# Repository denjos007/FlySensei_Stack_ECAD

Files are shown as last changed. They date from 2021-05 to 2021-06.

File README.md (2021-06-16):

PCB design of stackable controllers for blimps

Each stack contains a specified function for controlling a blimp

# Stacks
Below is the description of each stack

## RPi Stack
This stack takes care of the vision system for the blimp. The hardware integrates a Raspberry Pi CM4 with a Google Coral Accelerator Module. This combination will connect to upto 3 external cameras and process the image information. The system can implement machine vision algorithms like YOLO to process the scene and extract relevent information. 

## Actuation Stack

## Realtime Stack

## Sensing Stack

## Communication Stack

# Contributors
Joseph Prince Mathew - jprincem@masonlive.gmu.edu

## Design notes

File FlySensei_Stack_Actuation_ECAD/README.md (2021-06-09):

Actuation stack for the stackable blimp controller

# Functional Specifications
- PWM driver: PCA9685BS 16 channel 
- I2C control input with selectable channels
- 2S 3S and 4S LiPo input voltage capability
- 8 Servo channels with 5V power
- 8 BLDC or 4 Brushed motor channels with direct VBATT
- Optional 2S battery monitor: MAX17049G+T10
- Optional high current solder points for battery input

# Caution
- Check battery polarity before inserting the connecting the lipo battery
- When using 3S or higher voltage battery, remove the attached fuel gauge IC. Its rated only for 2S

# Contributors
Joseph Prince Mathew - jprincem@masonlive.gmu.edu

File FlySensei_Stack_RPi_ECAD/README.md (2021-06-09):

Stackable base board for the Raspberry Pi CM4 with an integrated AI co-processor

# Functional Specifications
- Raspberry Pi CM4 used as the main processor
- Google Coral used as the AI co-processor
- Selectable Power input from USB-C port and Battery input from stack headers
- Ethernet and camera FFC ports

# Contributors
Joseph Prince Mathew - jprincem@masonlive.gmu.edu

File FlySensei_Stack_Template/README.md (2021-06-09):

Template of the stack

Each stack contains 2x 20 pin connector with male pins on the top and the female pins on the bottom

# Usage

- Create a new PCB project in KiCAD
- Copy the schematic file and the PCB file to the project
- Rename the PCB file to the same name as the project
- Add the schematic of the connector to the main sheet as a hierarchical sheet

# Contributors
Joseph Prince Mathew - jprincem@masonlive.gmu.edu

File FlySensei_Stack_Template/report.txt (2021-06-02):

Info: Processing symbol 'C1:Capacitor_SMD:C_0402_1005Metric'.
Info: Processing symbol 'U16:Package_SO:SOIC-8-1EP_3.9x4.9mm_P1.27mm_EP2.95x4.9mm_Mask2.71x3.4mm_ThermalVias'.
Info: Processing symbol 'U10:Package_TO_SOT_SMD:SOT-23-5'.
Info: Processing symbol 'U9:Package_SON:USON-10_2.5x1.0mm_P0.5mm'.
Info: Processing symbol 'U8:Package_SON:USON-10_2.5x1.0mm_P0.5mm'.
Info: Processing symbol 'U7:Package_DFN_QFN_U:MPM3610_QFN-20_5x3mm'.
Info: Processing symbol 'U6:Package_DFN_QFN:Texas_X2QFN-12_1.6x1.6mm_P0.4mm'.
Info: Processing symbol 'U5:Package_TO_SOT_SMD:Texas_DRT-3'.
Info: Processing symbol 'C2:Capacitor_SMD:C_0402_1005Metric'.
Info: Processing symbol 'U4:AI_Coral:G313-06329-00'.
Info: Processing symbol 'U3:Package_TO_SOT_SMD:SOT-353_SC-70-5'.
Info: Processing symbol 'U2:Package_SO:SOIC-8W_5.3x5.3mm_P1.27mm'.
Info: Processing symbol 'U1:RPi_CM4IO:Raspberry-Pi-4-Compute-Module'.
Info: Processing symbol 'TP6:TestPoint:TestPoint_Pad_2.0x2.0mm'.
Info: Processing symbol 'TP4:TestPoint:TestPoint_Pad_2.0x2.0mm'.
Info: Processing symbol 'SW3:Button_Switch_SMD:SW_SPDT_PCM12'.
Info: Processing symbol 'C3:Capacitor_SMD:C_0402_1005Metric'.
Info: Processing symbol 'SW2:Button_Switch_SMD:SW_SPDT_PCM12'.
Info: Processing symbol 'SW1:Button_Switch_SMD:Panasonic_EVQPUL_EVQPUC'.
Info: Processing symbol 'R21:Resistor_SMD:R_0402_1005Metric'.
Info: Processing symbol 'R20:Resistor_SMD:R_0402_1005Metric'.
Info: Processing symbol 'R19:Resistor_SMD:R_0402_1005Metric'.
Info: Processing symbol 'R18:Resistor_SMD:R_0402_1005Metric'.
Info: Processing symbol 'R17:Resistor_SMD:R_0402_1005Metric'.
Info: Processing symbol 'C4:Capacitor_SMD:C_0402_1005Metric'.
Info: Processing symbol 'R16:Resistor_SMD:R_0402_1005Metric'.
Info: Processing symbol 'R15:Resistor_SMD:R_0402_1005Metric'.
Info: Processing symbol 'R14:Resistor_SMD:R_0402_1005Metric'.
Info: Processing symbol 'R13:Resistor_SMD:R_0402_1005Metric'.
Info: Processing symbol 'R12:Resistor_SMD:R_0402_1005Metric'.
Info: Processing symbol 'R11:Resistor_SMD:R_0402_1005Metric'.
Info: Processing symbol 'R10:Resistor_SMD:R_0402_1005Metric'.
Info: Processing symbol 'C5:Capacitor_SMD:C_0402_1005Metric'.
Info: Processing symbol 'R9:Resistor_SMD:R_0402_1005Metric'.
Info: Processing symbol 'R8:Resistor_SMD:R_0402_1005Metric'.
Info: Processing symbol 'R6:Resistor_SMD:R_0402_1005Metric'.
Info: Processing symbol 'R5:Resistor_SMD:R_0402_1005Metric'.
Info: Processing symbol 'R4:Resistor_SMD:R_0402_1005Metric'.
Info: Processing symbol 'R3:Resistor_SMD:R_0402_1005Metric'.
Info: Processing symbol 'R2:Resistor_SMD:R_0402_1005Metric'.
Info: Processing symbol 'C6:Capacitor_SMD:C_0402_1005Metric'.
Info: Processing symbol 'R1:Resistor_SMD:R_0402_1005Metric'.
Info: Processing symbol 'Q1:Package_TO_SOT_SMD:SOT-23'.
Info: Processing symbol 'L1:Inductor_SMD:L_Bourns_SRN6045TA'.
Info: Processing symbol 'JP6:Jumper:SolderJumper-2_P1.3mm_Open_RoundedPad1.0x1.5mm'.
Info: Processing symbol 'JP5:Jumper:SolderJumper-2_P1.3mm_Open_RoundedPad1.0x1.5mm'.
Info: Processing symbol 'JP4:Jumper:SolderJumper-2_P1.3mm_Open_RoundedPad1.0x1.5mm'.
Info: Processing symbol 'JP3:Jumper:SolderJumper-2_P1.3mm_Open_RoundedPad1.0x1.5mm'.
Info: Processing symbol 'C7:Capacitor_SMD:C_0402_1005Metric'.
Info: Processing symbol 'JP2:Jumper:SolderJumper-2_P1.3mm_Open_RoundedPad1.0x1.5mm'.
Info: Processing symbol 'JP1:Jumper:SolderJumper-2_P1.3mm_Open_RoundedPad1.0x1.5mm'.
Info: Processing symbol 'J10:CM4IO:SDCARD_MOLEX_503398-1892'.
Info: Processing symbol 'J9:Connector_FFC-FPC:Hirose_FH12-14S-0.5SH_1x14-1MP_P0.50mm_Horizontal'.
Info: Processing symbol 'J8:Connector_FFC-FPC:Hirose_FH12-22S-0.5SH_1x22-1MP_P0.50mm_Horizontal'.
Info: Processing symbol 'J7:Connector_FFC-FPC:Hirose_FH12-22S-0.5SH_1x22-1MP_P0.50mm_Horizontal'.
Info: Processing symbol 'J6:Connector_PinHeader_1.27mm:PinHeader_1x20_P1.27mm_Vertical_SMD_Pin1Left'.
Info: Processing symbol 'C8:Capacitor_SMD:C_0402_1005Metric'.
Info: Processing symbol 'J5:Connector_PinHeader_1.27mm:PinHeader_1x20_P1.27mm_Vertical_SMD_Pin1Right'.
Info: Processing symbol 'J4:Connector_PinHeader_1.27mm:PinHeader_1x20_P1.27mm_Vertical_SMD_Pin1Left'.
Info: Processing symbol 'J3:Connector_PinHeader_1.27mm:PinHeader_1x20_P1.27mm_Vertical_SMD_Pin1Right'.
Info: Processing symbol 'R7:Resistor_SMD:R_0402_1005Metric'.
Info: Processing symbol 'J2:Connector_USB:USB_C_Receptacle_XKB_U262-16XN-4BVC11'.
Info: Processing symbol 'J1:Connector_PinHeader_1.00mm:PinHeader_1x03_P1.00mm_Vertical'.
Info: Processing symbol 'D8:LED_SMD:LED_0603_1608Metric'.
Info: Processing symbol 'C9:Capacitor_SMD:C_0402_1005Metric'.
Info: Processing symbol 'D7:Diode_SMD:D_SMB'.
Info: Processing symbol 'D6:Diode_SMD:D_SMB'.
Info: Processing symbol 'D5:Diode_SMD:D_SMB'.
Info: Processing symbol 'D4:LED_SMD:LED_0603_1608Metric'.
Info: Processing symbol 'D3:LED_SMD:LED_0603_1608Metric'.
Info: Processing symbol 'D2:LED_SMD:LED_0603_1608Metric'.
Info: Processing symbol 'D1:LED_SMD:LED_0603_1608Metric'.
Info: Processing symbol 'C10:Capacitor_SMD:C_0402_1005Metric'.
Info: Processing symbol 'C27:Capacitor_SMD:C_0805_2012Metric'.
Info: Processing symbol 'C26:Capacitor_SMD:C_0805_2012Metric'.
Info: Processing symbol 'C25:Capacitor_SMD:C_0805_2012Metric'.
Info: Processing symbol 'C24:Capacitor_SMD:C_0805_2012Metric'.
Info: Processing symbol 'C23:Capacitor_SMD:C_0805_2012Metric'.
Info: Processing symbol 'C22:Capacitor_SMD:C_0402_1005Metric'.
Info: Processing symbol 'C21:Capacitor_SMD:C_0402_1005Metric'.
Info: Processing symbol 'C11:Capacitor_SMD:C_0603_1608Metric'.
Info: Processing symbol 'C20:Capacitor_SMD:C_0402_1005Metric'.
Info: Processing symbol 'C19:Capacitor_SMD:C_0603_1608Metric'.
Info: Processing symbol 'C18:Capacitor_Tantalum_SMD:CP_EIA-7343-31_Kemet-D'.
Info: Processing symbol 'C17:Capacitor_SMD:C_0402_1005Metric'.
Info: Processing symbol 'C16:Capacitor_SMD:C_0603_1608Metric'.
Info: Processing symbol 'C15:Capacitor_SMD:C_0402_1005Metric'.
Info: Processing symbol 'C14:Capacitor_SMD:C_0805_2012Metric'.
Info: Processing symbol 'C12:Capacitor_SMD:C_0603_1608Metric'.
Info: Processing symbol 'C13:Capacitor_SMD:C_0805_2012Metric'.
Changed REF** reference designator to C12.
Changed C12 value from C_0603_1608Metric to 1u 16V.
Updated C12 symbol association from  to /057c2e08-823a-4406-b5ca-db4e8c27b194/d5c9fad7-bc46-4f83-bd64-f66f1dbcdc59.
Updated C12 properties.
Connected C12 pin 1 to +5V.
Connected C12 pin 2 to GND.
Added C12 (footprint "Capacitor_SMD:C_0603_1608Metric").
Added C13 (footprint "Capacitor_SMD:C_0805_2012Metric").
Changed REF** reference designator to C13.
Changed C13 value from C_0805_2012Metric to 10u 35v.
Updated C13 symbol association from  to /0cf2b8c0-70f6-4976-95f7-88ea6c192189/00000000-0000-0000-0000-00005eb56b99.
Updated C13 properties.
Connected C13 pin 1 to +BATT.
Connected C13 pin 2 to GND.
Connected C11 pin 2 to GND.
Added C14 (footprint "Capacitor_SMD:C_0805_2012Metric").
Changed REF** reference designator to C14.
Changed C14 value from C_0805_2012Metric to 10u 35v.
Updated C14 symbol association from  to /0cf2b8c0-70f6-4976-95f7-88ea6c192189/00000000-0000-0000-0000-00005eb4cf69.
Updated C14 properties.
Connected C14 pin 1 to +BATT.
Connected C14 pin 2 to GND.
Connected C11 pin 1 to Net-(C11-Pad1).
Added C15 (footprint "Capacitor_SMD:C_0402_1005Metric").
Changed REF** reference designator to C15.
Changed C15 value from C_0402_1005Metric to 100n 35V.
Updated C15 symbol association from  to /0cf2b8c0-70f6-4976-95f7-88ea6c192189/00000000-0000-0000-0000-00005e540df2.
Updated C15 properties.
Connected C15 pin 1 to Net-(C15-Pad1).
Connected C15 pin 2 to Net-(C15-Pad2).
Updated C11 properties.
Added C16 (footprint "Capacitor_SMD:C_0603_1608Metric").
Changed REF** reference designator to C16.
Changed C16 value from C_0603_1608Metric to 10u 35V.
Updated C16 symbol association from  to /0cf2b8c0-70f6-4976-95f7-88ea6c192189/0d5ad291-fce2-4c53-b48f-1c66806904ff.
Updated C16 properties.
Connected C16 pin 1 to +BATT.
Connected C16 pin 2 to GND.
Updated C11 symbol association from  to /057c2e08-823a-4406-b5ca-db4e8c27b194/cf37d5d3-b56f-4aae-943b-4b63578a7e71.
Added C17 (footprint "Capacitor_SMD:C_0402_1005Metric").
Changed REF** reference designator to C17.
Changed C17 value from C_0402_1005Metric to 100n 35V.
Updated C17 symbol association from  to /0cf2b8c0-70f6-4976-95f7-88ea6c192189/00000000-0000-0000-0000-00005e540dfb.
Updated C17 properties.
Connected C17 pin 1 to Net-(C17-Pad1).
Connected C17 pin 2 to GND.
Changed C11 value from C_0603_1608Metric to 22u 16V.
Added C18 (footprint "Capacitor_Tantalum_SMD:CP_EIA-7343-31_Kemet-D").
Changed REF** reference designator to C18.
Changed C18 value from CP_EIA-7343-31_Kemet-D to 100uF.
Updated C18 symbol association from  to /0cf2b8c0-70f6-4976-95f7-88ea6c192189/37be3783-986e-41bc-a074-efadea452183.
Updated C18 properties.
Connected C18 pin 1 to Net-(C18-Pad1).
Connected C18 pin 2 to GND.
Changed REF** reference designator to C11.
Added C19 (footprint "Capacitor_SMD:C_0603_1608Metric").
Changed REF** reference designator to C19.
Changed C19 value from C_0603_1608Metric to 22u 16V.
Updated C19 symbol association from  to /0cf2b8c0-70f6-4976-95f7-88ea6c192189/f4fe2ad8-9f7d-486e-9b01-b41b7db66e44.
Updated C19 properties.
Connected C19 pin 1 to +3V3.
Connected C19 pin 2 to GND.
Added C11 (footprint "Capacitor_SMD:C_0603_1608Metric").
Added C20 (footprint "Capacitor_SMD:C_0402_1005Metric").
Changed REF** reference designator to C20.
Changed C20 value from C_0402_1005Metric to 1nf 16V.
Updated C20 symbol association from  to /0cf2b8c0-70f6-4976-95f7-88ea6c192189/00000000-0000-0000-0000-00005e540df8.
Updated C20 properties.
Connected C20 pin 1 to Net-(C20-Pad1).
Connected C20 pin 2 to GND.
Connected C10 pin 2 to GND.
Added C21 (footprint "Capacitor_SMD:C_0402_1005Metric").
Changed REF** reference designator to C21.
Changed C21 value from C_0402_1005Metric to 1.2nF 16V.
Updated C21 symbol association from  to /0cf2b8c0-70f6-4976-95f7-88ea6c192189/00000000-0000-0000-0000-00005e540df7.
Updated C21 properties.
Connected C21 pin 1 to Net-(C21-Pad1).
Connected C21 pin 2 to GND.
Connected C10 pin 1 to +3V3.
Added C22 (footprint "Capacitor_SMD:C_0402_1005Metric").
Changed REF** reference designator to C22.
Changed C22 value from C_0402_1005Metric to 1nf 16V.
Updated C22 symbol association from  to /0cf2b8c0-70f6-4976-95f7-88ea6c192189/00000000-0000-0000-0000-00005e540df4.
Updated C22 properties.
Connected C22 pin 1 to Net-(C18-Pad1).
Connected C22 pin 2 to Net-(C22-Pad2).
Updated C10 properties.
Added C23 (footprint "Capacitor_SMD:C_0805_2012Metric").
Changed REF** reference designator to C23.
Changed C23 value from C_0805_2012Metric to 22u 16V.
Updated C23 symbol association from  to /0cf2b8c0-70f6-4976-95f7-88ea6c192189/00000000-0000-0000-0000-00005d3289ab.
Updated C23 properties.
Connected C23 pin 1 to Net-(C18-Pad1).
Connected C23 pin 2 to GND.
Updated C10 symbol association from  to /c7aadd96-de8c-4974-aee8-6d5527743de5/b0267f50-fd0c-4a5f-b7d1-92f9a74be421.
Added C24 (footprint "Capacitor_SMD:C_0805_2012Metric").
Changed REF** reference designator to C24.
Changed C24 value from C_0805_2012Metric to 22u 16V.
Updated C24 symbol association from  to /0cf2b8c0-70f6-4976-95f7-88ea6c192189/00000000-0000-0000-0000-00005d3289b2.
Updated C24 properties.
Connected C24 pin 1 to Net-(C18-Pad1).
Connected C24 pin 2 to GND.
Changed C10 value from C_0402_1005Metric to 0u1 6.3V.
Added C25 (footprint "Capacitor_SMD:C_0805_2012Metric").
Changed REF** reference designator to C25.
Changed C25 value from C_0805_2012Metric to 22u 16V.
Updated C25 symbol association from  to /0cf2b8c0-70f6-4976-95f7-88ea6c192189/00000000-0000-0000-0000-00005d3289b8.
Updated C25 properties.
Connected C25 pin 1 to Net-(C18-Pad1).
Connected C25 pin 2 to GND.
Changed REF** reference designator to C10.
Added C26 (footprint "Capacitor_SMD:C_0805_2012Metric").
Changed REF** reference designator to C26.
Changed C26 value from C_0805_2012Metric to 22u.
Updated C26 symbol association from  to /f22911d6-fd0b-420b-886b-10dcff84029c/93127e37-2f19-438d-a456-8a96f2977297.
Updated C26 properties.
Connected C26 pin 1 to +BATT.
Connected C26 pin 2 to GND.
Added C10 (footprint "Capacitor_SMD:C_0402_1005Metric").
Added C27 (footprint "Capacitor_SMD:C_0805_2012Metric").
Changed REF** reference designator to C27.
Changed C27 value from C_0805_2012Metric to 10u.
Updated C27 symbol association from  to /b1d9abd2-56b2-476f-ba8d-e6505e2da0de/7aa47e22-220a-48de-a0dc-e60b4a80156a.
Updated C27 properties.
Connected C27 pin 1 to /SD Card/SD_PWR.
Connected C27 pin 2 to GND.
Connected C9 pin 2 to GND.
Added D1 (footprint "LED_SMD:LED_0603_1608Metric").
Changed REF** reference designator to D1.
Changed D1 value from LED_0603_1608Metric to LED_GRN.
Updated D1 symbol association from  to /93e7d8cf-e360-4b54-86be-d58fb9455bdf/d052e667-c78d-4c60-9067-dea9ab9f9831.
Updated D1 properties.
Connected D1 pin 1 to Net-(D1-Pad1).
Connected D1 pin 2 to +3V3_RPI.
Connected C9 pin 1 to +3V3.
Added D2 (footprint "LED_SMD:LED_0603_1608Metric").
Changed REF** reference designator to D2.
Changed D2 value from LED_0603_1608Metric to LED_GRN.
Updated D2 symbol association from  to /93e7d8cf-e360-4b54-86be-d58fb9455bdf/5d8d864f-70b6-4a40-8cab-c69691953af5.
Updated D2 properties.
Connected D2 pin 1 to Net-(D2-Pad1).
Connected D2 pin 2 to +3V3_RPI.
Updated C9 properties.
Added D3 (footprint "LED_SMD:LED_0603_1608Metric").
Changed REF** reference designator to D3.
Changed D3 value from LED_0603_1608Metric to LED_AMB.
Updated D3 symbol association from  to /93e7d8cf-e360-4b54-86be-d58fb9455bdf/27de79ba-83bf-482b-9f05-30a12075cb2a.
Updated D3 properties.
Connected D3 pin 1 to Net-(D3-Pad1).
Connected D3 pin 2 to +3V3_RPI.
Updated C9 symbol association from  to /c7aadd96-de8c-4974-aee8-6d5527743de5/035c14f8-ab75-4ff6-90a5-e33b5679a37f.
Added D4 (footprint "LED_SMD:LED_0603_1608Metric").
Changed REF** reference designator to D4.
Changed D4 value from LED_0603_1608Metric to LED_RED.
Updated D4 symbol association from  to /93e7d8cf-e360-4b54-86be-d58fb9455bdf/b7a968bb-c5ee-44dd-8959-c6f6e151e9ab.
Updated D4 properties.
Connected D4 pin 1 to Net-(D4-Pad1).
Connected D4 pin 2 to +3V3_RPI.
Changed C9 value from C_0402_1005Metric to 0u1 6.3V.
Added D5 (footprint "Diode_SMD:D_SMB").
Changed REF** reference designator to D5.
Changed D5 value from D_SMB to D_Schottky.
Updated D5 symbol association from  to /057c2e08-823a-4406-b5ca-db4e8c27b194/81568044-992c-48f2-a54a-9e9377f4d5ae.
Updated D5 properties.
Connected D5 pin 1 to +5V.
Connected D5 pin 2 to Net-(C11-Pad1).
Changed REF** reference designator to C9.
Added D6 (footprint "Diode_SMD:D_SMB").
Changed REF** reference designator to D6.
Changed D6 value from D_SMB to D_Schottky.
Updated D6 symbol association from  to /0cf2b8c0-70f6-4976-95f7-88ea6c192189/ed8ba917-dfd4-4435-9898-75160a2297d1.
Updated D6 properties.
Connected D6 pin 1 to +5V.
Connected D6 pin 2 to Net-(C18-Pad1).
Added C9 (footprint "Capacitor_SMD:C_0402_1005Metric").
Added D7 (footprint "Diode_SMD:D_SMB").
Changed REF** reference designator to D7.
Changed D7 value from D_SMB to D_Schottky.
Updated D7 symbol association from  to /f22911d6-fd0b-420b-886b-10dcff84029c/0b2db708-50f7-447f-92a1-9296f2459b91.
Updated D7 properties.
Connected D7 pin 1 to +BATT.
Connected D7 pin 2 to /Stacking Connectors/BATT_IN.
Connected C8 pin 2 to GND.
Added D8 (footprint "LED_SMD:LED_0603_1608Metric").
Changed REF** reference designator to D8.
Changed D8 value from LED_0603_1608Metric to W_LED.
Updated D8 symbol association from  to /93e7d8cf-e360-4b54-86be-d58fb9455bdf/5fc6c698-fa36-406b-8e10-f746facb42c5.
Updated D8 properties.
Connected D8 pin 1 to Net-(D8-Pad1).
Connected D8 pin 2 to Net-(D8-Pad2).
Connected C8 pin 1 to +3V3.
Added J1 (footprint "Connector_PinHeader_1.00mm:PinHeader_1x03_P1.00mm_Vertical").
Changed REF** reference designator to J1.
Changed J1 value from PinHeader_1x03_P1.00mm_Vertical to Conn_01x03.
Updated J1 symbol association from  to /93e7d8cf-e360-4b54-86be-d58fb9455bdf/e53ead3b-26db-4a23-bd2d-10031139ddc5.
Updated J1 properties.
Connected J1 pin 1 to /RPi_CM4/RPI_RUN_PG.
Connected J1 pin 2 to GND.
Connected J1 pin 3 to /RPi_CM4/RPI_GLOBL_EN.
Updated C8 properties.
Added J2 (footprint "Connector_USB:USB_C_Receptacle_XKB_U262-16XN-4BVC11").
Changed REF** reference designator to J2.
Changed J2 value from USB_C_Receptacle_XKB_U262-16XN-4BVC11 to USB_C_Receptacle_USB2.0.
Updated J2 symbol association from  to /057c2e08-823a-4406-b5ca-db4e8c27b194/14bf70aa-48dc-42ff-af02-dd620e4b800d.
Updated J2 properties.
Connected J2 pin S1 to unconnected-(J2-PadS1).
Connected J2 pin S1 to unconnected-(J2-PadS1).
Connected J2 pin S1 to unconnected-(J2-PadS1).
Connected J2 pin S1 to unconnected-(J2-PadS1).
Connected J2 pin B1 to GND.
Connected J2 pin B4 to Net-(C11-Pad1).
Connected J2 pin B5 to Net-(J2-PadB5).
Connected J2 pin A8 to unconnected-(J2-PadA8).
Connected J2 pin B6 to /RPi_CM4/USB_DP.
Connected J2 pin A7 to /RPi_CM4/USB_DN.
Connected J2 pin A6 to /RPi_CM4/USB_DP.
Connected J2 pin B7 to /RPi_CM4/USB_DN.
Connected J2 pin A5 to Net-(J2-PadA5).
Updated C8 symbol association from  to /c7aadd96-de8c-4974-aee8-6d5527743de5/35e6c8af-12af-4b13-9694-213bb1cf0153.
Connected J2 pin A4 to Net-(C11-Pad1).
Connected J2 pin A1 to GND.
Connected J2 pin B12 to GND.
Connected J2 pin B9 to Net-(C11-Pad1).
Connected J2 pin A9 to Net-(C11-Pad1).
Connected J2 pin A12 to GND.
Changed C8 value from C_0402_1005Metric to 0u1 6.3V.
Added J3 (footprint "Connector_PinHeader_1.27mm:PinHeader_1x20_P1.27mm_Vertical_SMD_Pin1Right").
Changed REF** reference designator to J3.
Changed J3 value from PinHeader_1x20_P1.27mm_Vertical_SMD_Pin1Right to Conn_01x20_Female.
Updated J3 symbol association from  to /f22911d6-fd0b-420b-886b-10dcff84029c/730ab321-7c86-4037-aece-98780bac3f9a.
Updated J3 properties.
Connected J3 pin 2 to /Stacking Connectors/BATT_IN.
Connected J3 pin 4 to GND.
Connected J3 pin 6 to /RPi_CM4/GPIO_1.
Connected J3 pin 8 to /RPi_CM4/SPI0.MISO.
Connected J3 pin 10 to /RPi_CM4/SPI0.CS0.
Connected J3 pin 12 to /RPi_CM4/SPI0.CS2.
Connected J3 pin 14 to GND.
Connected J3 pin 16 to /RPi_CM4/SPI1.MISO.
Connected J3 pin 18 to /RPi_CM4/SPI1.CS0.
Connected J3 pin 20 to GND.
Connected J3 pin 1 to /Stacking Connectors/BATT_IN.
Connected J3 pin 3 to GND.
Connected J3 pin 5 to /RPi_CM4/GPIO_0.
Connected J3 pin 7 to /RPi_CM4/SPI0.MOSI.
Connected J3 pin 9 to /RPi_CM4/SPI0.CLK.
Connected J3 pin 11 to /RPi_CM4/SPI0.CS1.
Connected J3 pin 13 to /RPi_CM4/SPI0.CS3.
Connected J3 pin 15 to /RPi_CM4/SPI1.MOSI.
Connected J3 pin 17 to /RPi_CM4/SPI1.CLK.
Connected J3 pin 19 to /RPi_CM4/SPI1.CS1.
Changed REF** reference designator to C8.
Added J4 (footprint "Connector_PinHeader_1.27mm:PinHeader_1x20_P1.27mm_Vertical_SMD_Pin1Left").
Changed REF** reference designator to J4.
Changed J4 value from PinHeader_1x20_P1.27mm_Vertical_SMD_Pin1Left to Conn_01x20_Male.
Updated J4 symbol association from  to /f22911d6-fd0b-420b-886b-10dcff84029c/8999cfdc-1a52-4c6c-8d6f-7db9d488c1ed.
Updated J4 properties.
Connected J4 pin 1 to /Stacking Connectors/BATT_IN.
Connected J4 pin 3 to GND.
Connected J4 pin 5 to /RPi_CM4/GPIO_0.
Connected J4 pin 7 to /RPi_CM4/SPI0.MOSI.
Connected J4 pin 9 to /RPi_CM4/SPI0.CLK.
Connected J4 pin 11 to /RPi_CM4/SPI0.CS1.
Connected J4 pin 13 to /RPi_CM4/SPI0.CS3.
Connected J4 pin 15 to /RPi_CM4/SPI1.MOSI.
Connected J4 pin 17 to /RPi_CM4/SPI1.CLK.
Connected J4 pin 19 to /RPi_CM4/SPI1.CS1.
Connected J4 pin 2 to /Stacking Connectors/BATT_IN.
Connected J4 pin 4 to GND.
Connected J4 pin 6 to /RPi_CM4/GPIO_1.
Connected J4 pin 8 to /RPi_CM4/SPI0.MISO.
Connected J4 pin 10 to /RPi_CM4/SPI0.CS0.
Connected J4 pin 12 to /RPi_CM4/SPI0.CS2.
Connected J4 pin 14 to GND.
Connected J4 pin 16 to /RPi_CM4/SPI1.MISO.
Connected J4 pin 18 to /RPi_CM4/SPI1.CS0.
Connected J4 pin 20 to GND.
Added C8 (footprint "Capacitor_SMD:C_0402_1005Metric").
Added J5 (footprint "Connector_PinHeader_1.27mm:PinHeader_1x20_P1.27mm_Vertical_SMD_Pin1Right").
Changed REF** reference designator to J5.
Changed J5 value from PinHeader_1x20_P1.27mm_Vertical_SMD_Pin1Right to Conn_01x20_Female.
Updated J5 symbol association from  to /f22911d6-fd0b-420b-886b-10dcff84029c/7beed154-96e9-49c8-b518-4b3691163b95.
Updated J5 properties.
Connected J5 pin 2 to /Stacking Connectors/BATT_IN.
Connected J5 pin 4 to GND.
Connected J5 pin 6 to /RPi_CM4/GPIO_3.
Connected J5 pin 8 to /RPi_CM4/GPIO_5.
Connected J5 pin 10 to /RPi_CM4/GPIO_7.
Connected J5 pin 12 to /RPi_CM4/I2C0.SCL.
Connected J5 pin 14 to /Stacking Connectors/I2C1.SCL.
Connected J5 pin 16 to GND.
Connected J5 pin 18 to /RPi_CM4/UART0.RX.
Connected J5 pin 20 to /RPi_CM4/UART1.RX.
Connected J5 pin 1 to /Stacking Connectors/BATT_IN.
Connected J5 pin 3 to GND.
Connected J5 pin 5 to /RPi_CM4/GPIO_2.
Connected J5 pin 7 to /RPi_CM4/GPIO_4.
Connected J5 pin 9 to /RPi_CM4/GPIO_6.
Connected J5 pin 11 to GND.
Connected J5 pin 13 to /RPi_CM4/I2C0.SDA.
Connected J5 pin 15 to /Stacking Connectors/I2C1.SDA.
Connected J5 pin 17 to /RPi_CM4/UART0.TX.
Connected J5 pin 19 to /RPi_CM4/UART1.TX.
Connected C7 pin 2 to GND.
Added J6 (footprint "Connector_PinHeader_1.27mm:PinHeader_1x20_P1.27mm_Vertical_SMD_Pin1Left").
Changed REF** reference designator to J6.
Changed J6 value from PinHeader_1x20_P1.27mm_Vertical_SMD_Pin1Left to Conn_01x20_Male.
Updated J6 symbol association from  to /f22911d6-fd0b-420b-886b-10dcff84029c/d6cef596-d8af-42ab-a0b6-04219f1f1742.
Updated J6 properties.
Connected J6 pin 1 to /Stacking Connectors/BATT_IN.
Connected J6 pin 3 to GND.
Connected J6 pin 5 to /RPi_CM4/GPIO_2.
Connected J6 pin 7 to /RPi_CM4/GPIO_4.
Connected J6 pin 9 to /RPi_CM4/GPIO_6.
Connected J6 pin 11 to GND.
Connected J6 pin 13 to /RPi_CM4/I2C0.SDA.
Connected J6 pin 15 to /Stacking Connectors/I2C1.SDA.
Connected J6 pin 17 to /RPi_CM4/UART0.TX.
Connected J6 pin 19 to /RPi_CM4/UART1.TX.
Connected J6 pin 2 to /Stacking Connectors/BATT_IN.
Connected J6 pin 4 to GND.
Connected J6 pin 6 to /RPi_CM4/GPIO_3.
Connected J6 pin 8 to /RPi_CM4/GPIO_5.
Connected J6 pin 10 to /RPi_CM4/GPIO_7.
Connected J6 pin 12 to /RPi_CM4/I2C0.SCL.
Connected J6 pin 14 to /Stacking Connectors/I2C1.SCL.
Connected J6 pin 16 to GND.
Connected J6 pin 18 to /RPi_CM4/UART0.RX.
Connected J6 pin 20 to /RPi_CM4/UART1.RX.
Connected C7 pin 1 to +3V3.
Added J7 (footprint "Connector_FFC-FPC:Hirose_FH12-22S-0.5SH_1x22-1MP_P0.50mm_Horizontal").
Changed REF** reference designator to J7.
Changed J7 value from Hirose_FH12-22S-0.5SH_1x22-1MP_P0.50mm_Horizontal to Conn_01x22_Female.
Updated J7 symbol association from  to /1a1df624-ea52-444e-8eb0-2f13ef4aac9c/b3fac725-0c5e-42cc-9b85-f37d2753b6b5.
Updated J7 properties.
Connected J7 pin 1 to GND.
Connected J7 pin 2 to /High Speed Interfaces/CAM0_MIPI.D0_N.
Connected J7 pin 3 to /High Speed Interfaces/CAM0_MIPI.D0_P.
Connected J7 pin 4 to GND.
Connected J7 pin 5 to /High Speed Interfaces/CAM0_MIPI.D1_N.
Connected J7 pin 6 to /High Speed Interfaces/CAM0_MIPI.D1_P.
Connected J7 pin 7 to GND.
Connected J7 pin 8 to /High Speed Interfaces/CAM0_MIPI.C_N.
Connected J7 pin 9 to /High Speed Interfaces/CAM0_MIPI.C_P.
Connected J7 pin 10 to GND.
Connected J7 pin 11 to unconnected-(J7-Pad11).
Connected J7 pin 12 to unconnected-(J7-Pad12).
Connected J7 pin 13 to GND.
Connected J7 pin 14 to unconnected-(J7-Pad14).
Connected J7 pin 15 to unconnected-(J7-Pad15).
Connected J7 pin 16 to GND.
Connected J7 pin 17 to /High Speed Interfaces/CAM_GPIO.
Connected J7 pin 18 to unconnected-(J7-Pad18).
Connected J7 pin 19 to GND.
Connected J7 pin 20 to /High Speed Interfaces/CAM0_SCL.
Connected J7 pin 21 to /High Speed Interfaces/CAM0_SDA.
Connected J7 pin 22 to +3V3.
Updated C7 properties.
Added J8 (footprint "Connector_FFC-FPC:Hirose_FH12-22S-0.5SH_1x22-1MP_P0.50mm_Horizontal").
Changed REF** reference designator to J8.
Changed J8 value from Hirose_FH12-22S-0.5SH_1x22-1MP_P0.50mm_Horizontal to Conn_01x22_Female.
Updated J8 symbol association from  to /1a1df624-ea52-444e-8eb0-2f13ef4aac9c/320604ed-1bea-420b-bb1c-2d498855f18f.
Updated J8 properties.
Connected J8 pin 1 to GND.
Connected J8 pin 2 to /High Speed Interfaces/CAM1_MIPI.D0_N.
Connected J8 pin 3 to /High Speed Interfaces/CAM1_MIPI.D0_P.
Connected J8 pin 4 to GND.
Connected J8 pin 5 to /High Speed Interfaces/CAM1_MIPI.D1_N.
Connected J8 pin 6 to /High Speed Interfaces/CAM1_MIPI.D1_P.
Connected J8 pin 7 to GND.
Connected J8 pin 8 to /High Speed Interfaces/CAM1_MIPI.C_N.
Connected J8 pin 9 to /High Speed Interfaces/CAM1_MIPI.C_P.
Connected J8 pin 10 to GND.
Connected J8 pin 11 to /High Speed Interfaces/CAM1_MIPI.D2_N.
Connected J8 pin 12 to /High Speed Interfaces/CAM1_MIPI.D2_P.
Connected J8 pin 13 to GND.
Connected J8 pin 14 to /High Speed Interfaces/CAM1_MIPI.D3_N.
Connected J8 pin 15 to /High Speed Interfaces/CAM1_MIPI.D3_P.
Connected J8 pin 16 to GND.
Connected J8 pin 17 to /High Speed Interfaces/CAM_GPIO.
Connected J8 pin 18 to unconnected-(J8-Pad18).
Connected J8 pin 19 to GND.
Connected J8 pin 20 to /High Speed Interfaces/CAM1_SCL.
Connected J8 pin 21 to /High Speed Interfaces/CAM1_SDA.
Connected J8 pin 22 to +3V3.
Updated C7 symbol association from  to /c7aadd96-de8c-4974-aee8-6d5527743de5/72f7f23e-6b73-4163-b333-bc0cda4ebd4c.
Added J9 (footprint "Connector_FFC-FPC:Hirose_FH12-14S-0.5SH_1x14-1MP_P0.50mm_Horizontal").
Changed REF** reference designator to J9.
Changed J9 value from Hirose_FH12-14S-0.5SH_1x14-1MP_P0.50mm_Horizontal to Conn_01x14_Female.
Updated J9 symbol association from  to /1a1df624-ea52-444e-8eb0-2f13ef4aac9c/fd6e2cfa-b86c-4352-aba3-aee09704695a.
Updated J9 properties.
Connected J9 pin 1 to GND.
Connected J9 pin 2 to /High Speed Interfaces/ETH.0_N.
Connected J9 pin 3 to /High Speed Interfaces/ETH.0_P.
Connected J9 pin 4 to GND.
Connected J9 pin 5 to /High Speed Interfaces/ETH.1_N.
Connected J9 pin 6 to /High Speed Interfaces/ETH.1_P.
Connected J9 pin 7 to GND.
Connected J9 pin 8 to /High Speed Interfaces/ETH.2_N.
Connected J9 pin 9 to /High Speed Interfaces/ETH.2_P.
Connected J9 pin 10 to GND.
Connected J9 pin 11 to /High Speed Interfaces/ETH.3_N.
Connected J9 pin 12 to /High Speed Interfaces/ETH.3_P.
Connected J9 pin 13 to GND.
Connected J9 pin 14 to GND.
Changed C7 value from C_0402_1005Metric to 0u1 6.3V.
Connected U16 pin 9 to GND.
Changed REF** reference designator to C7.
Added JP1 (footprint "Jumper:SolderJumper-2_P1.3mm_Open_RoundedPad1.0x1.5mm").
Changed REF** reference designator to JP1.
Changed JP1 value from SolderJumper-2_P1.3mm_Open_RoundedPad1.0x1.5mm to SolderJumper_2_Open.
Updated JP1 symbol association from  to /93e7d8cf-e360-4b54-86be-d58fb9455bdf/dc7345bb-3f89-4cb9-ab2b-c1238f3023d7.
Updated JP1 properties.
Removed JP1 'exclude from BOM' fabrication attribute.
Connected JP1 pin 1 to GND.
Connected JP1 pin 2 to Net-(JP1-Pad2).
Added C7 (footprint "Capacitor_SMD:C_0402_1005Metric").
Added JP2 (footprint "Jumper:SolderJumper-2_P1.3mm_Open_RoundedPad1.0x1.5mm").
Changed REF** reference designator to JP2.
Changed JP2 value from SolderJumper-2_P1.3mm_Open_RoundedPad1.0x1.5mm to SolderJumper_2_Open.
Updated JP2 symbol association from  to /93e7d8cf-e360-4b54-86be-d58fb9455bdf/a9cff73d-1108-4c23-872b-0f1677a704dc.
Updated JP2 properties.
Removed JP2 'exclude from BOM' fabrication attribute.
Connected JP2 pin 1 to GND.
Connected JP2 pin 2 to Net-(JP2-Pad2).
Connected C6 pin 2 to GND.
Added JP3 (footprint "Jumper:SolderJumper-2_P1.3mm_Open_RoundedPad1.0x1.5mm").
Changed REF** reference designator to JP3.
Changed JP3 value from SolderJumper-2_P1.3mm_Open_RoundedPad1.0x1.5mm to SolderJumper_2_Open.
Updated JP3 symbol association from  to /93e7d8cf-e360-4b54-86be-d58fb9455bdf/d1a86628-3b71-4a5e-80a1-6db9b7a2cd90.
Updated JP3 properties.
Removed JP3 'exclude from BOM' fabrication attribute.
Connected JP3 pin 1 to GND.
Connected JP3 pin 2 to Net-(JP3-Pad2).
Connected C6 pin 1 to +3V3.
Added JP4 (footprint "Jumper:SolderJumper-2_P1.3mm_Open_RoundedPad1.0x1.5mm").
Changed REF** reference designator to JP4.
Changed JP4 value from SolderJumper-2_P1.3mm_Open_RoundedPad1.0x1.5mm to SolderJumper_2_Open.
Updated JP4 symbol association from  to /93e7d8cf-e360-4b54-86be-d58fb9455bdf/1a89e859-74bb-4a5a-8b47-c0029b505993.
Updated JP4 properties.
Removed JP4 'exclude from BOM' fabrication attribute.
Connected JP4 pin 1 to GND.
Connected JP4 pin 2 to Net-(JP4-Pad2).
Updated C6 properties.
Added JP5 (footprint "Jumper:SolderJumper-2_P1.3mm_Open_RoundedPad1.0x1.5mm").
Changed REF** reference designator to JP5.
Changed JP5 value from SolderJumper-2_P1.3mm_Open_RoundedPad1.0x1.5mm to SolderJumper_2_Open.
Updated JP5 symbol association from  to /93e7d8cf-e360-4b54-86be-d58fb9455bdf/cbe39c9d-86bc-4e97-a787-66fb16316087.
Updated JP5 properties.
Removed JP5 'exclude from BOM' fabrication attribute.
Connected JP5 pin 1 to Net-(JP5-Pad1).
Connected JP5 pin 2 to /RPi_CM4/RPI_GLOBL_EN.
Updated C6 symbol association from  to /c7aadd96-de8c-4974-aee8-6d5527743de5/12596052-1343-483f-97a7-aa12fbc61fde.
Added JP6 (footprint "Jumper:SolderJumper-2_P1.3mm_Open_RoundedPad1.0x1.5mm").
Changed REF** reference designator to JP6.
Changed JP6 value from SolderJumper-2_P1.3mm_Open_RoundedPad1.0x1.5mm to SolderJumper_2_Open.
Updated JP6 symbol association from  to /057c2e08-823a-4406-b5ca-db4e8c27b194/55ecf1c4-1c2e-4d7b-be73-50efe6cf1549.
Updated JP6 properties.
Removed JP6 'exclude from BOM' fabrication attribute.
Connected JP6 pin 1 to Net-(JP6-Pad1).
Connected JP6 pin 2 to Net-(JP6-Pad2).
Changed C6 value from C_0402_1005Metric to 0u1 6.3V.
Added L1 (footprint "Inductor_SMD:L_Bourns_SRN6045TA").
Changed REF** reference designator to L1.
Changed L1 value from L_Bourns_SRN6045TA to SRN6045TA-3R3Y.
Updated L1 symbol association from  to /0cf2b8c0-70f6-4976-95f7-88ea6c192189/00000000-0000-0000-0000-00005e540df6.
Updated L1 properties.
Connected L1 pin 1 to Net-(L1-Pad1).
Connected L1 pin 2 to Net-(C18-Pad1).
Changed REF** reference designator to C6.
Added Q1 (footprint "Package_TO_SOT_SMD:SOT-23").
Changed REF** reference designator to Q1.
Changed Q1 value from SOT-23 to Q_NMOS_GSD.
Updated Q1 symbol association from  to /93e7d8cf-e360-4b54-86be-d58fb9455bdf/17b4384f-a1ec-4bdc-880b-a2a10d4dbdf2.
Updated Q1 properties.
Connected Q1 pin 1 to Net-(Q1-Pad1).
Connected Q1 pin 2 to GND.
Connected Q1 pin 3 to Net-(JP5-Pad1).
Added C6 (footprint "Capacitor_SMD:C_0402_1005Metric").
Added R1 (footprint "Resistor_SMD:R_0402_1005Metric").
Changed REF** reference designator to R1.
Changed R1 value from R_0402_1005Metric to 270R.
Updated R1 symbol association from  to /93e7d8cf-e360-4b54-86be-d58fb9455bdf/4cd007f1-dd88-47c3-99c9-8fd32a0ae91f.
Updated R1 properties.
Connected R1 pin 1 to Net-(D1-Pad1).
Connected R1 pin 2 to /RPi_CM4/RPI_nLED_ACT.
Connected C5 pin 2 to GND.
Added R2 (footprint "Resistor_SMD:R_0402_1005Metric").
Changed REF** reference designator to R2.
Changed R2 value from R_0402_1005Metric to 270R.
Updated R2 symbol association from  to /93e7d8cf-e360-4b54-86be-d58fb9455bdf/28a81803-4a19-47c3-aa78-db5d0bfc86a4.
Updated R2 properties.
Connected R2 pin 1 to Net-(D2-Pad1).
Connected R2 pin 2 to /RPi_CM4/ETH_nLED1.
Connected C5 pin 1 to +3V3.
Added R3 (footprint "Resistor_SMD:R_0402_1005Metric").
Changed REF** reference designator to R3.
Changed R3 value from R_0402_1005Metric to 270R.
Updated R3 symbol association from  to /93e7d8cf-e360-4b54-86be-d58fb9455bdf/6c87f5ba-c475-4100-a9d7-36ca2d5a00b7.
Updated R3 properties.
Connected R3 pin 1 to Net-(D3-Pad1).
Connected R3 pin 2 to /RPi_CM4/ETH_nLED2.
Updated C5 properties.
Added R4 (footprint "Resistor_SMD:R_0402_1005Metric").
Changed REF** reference designator to R4.
Changed R4 value from R_0402_1005Metric to 270R.
Updated R4 symbol association from  to /93e7d8cf-e360-4b54-86be-d58fb9455bdf/14145cb0-71f3-4bf1-813f-8adaf3854fa8.
Updated R4 properties.
Connected R4 pin 1 to Net-(D4-Pad1).
Connected R4 pin 2 to Net-(R4-Pad2).
Updated C5 symbol association from  to /c7aadd96-de8c-4974-aee8-6d5527743de5/105b9c96-a82a-458d-a6a9-6413d384d585.
Added R5 (footprint "Resistor_SMD:R_0402_1005Metric").
Changed REF** reference designator to R5.
Changed R5 value from R_0402_1005Metric to 4.7K.
Updated R5 symbol association from  to /057c2e08-823a-4406-b5ca-db4e8c27b194/8bb5f324-eca5-4a71-a945-49abde35dc40.
Updated R5 properties.
Connected R5 pin 1 to Net-(R5-Pad1).
Connected R5 pin 2 to +5V.
Changed C5 value from C_0402_1005Metric to 0u1 6.3V.
Added R6 (footprint "Resistor_SMD:R_0402_1005Metric").
Changed REF** reference designator to R6.
Changed R6 value from R_0402_1005Metric to 900K.
Updated R6 symbol association from  to /057c2e08-823a-4406-b5ca-db4e8c27b194/5374aba3-9d0e-4d4b-abab-195b14aafaf9.
Updated R6 properties.
Connected R6 pin 1 to Net-(R6-Pad1).
Connected R6 pin 2 to Net-(C11-Pad1).
Connected J2 pin B8 to unconnected-(J2-PadB8).
Added R7 (footprint "Resistor_SMD:R_0402_1005Metric").
Changed REF** reference designator to R7.
Changed R7 value from R_0402_1005Metric to 50K.
Updated R7 symbol association from  to /057c2e08-823a-4406-b5ca-db4e8c27b194/b83d1370-c1b1-4350-a349-39dd7788a953.
Updated R7 properties.
Connected R7 pin 1 to +5V.
Connected R7 pin 2 to Net-(R7-Pad2).
Changed REF** reference designator to C5.
Added R8 (footprint "Resistor_SMD:R_0402_1005Metric").
Changed REF** reference designator to R8.
Changed R8 value from R_0402_1005Metric to 10R.
Updated R8 symbol association from  to /0cf2b8c0-70f6-4976-95f7-88ea6c192189/00000000-0000-0000-0000-00005e540df3.
Updated R8 properties.
Connected R8 pin 1 to Net-(L1-Pad1).
Connected R8 pin 2 to Net-(C15-Pad1).
Added C5 (footprint "Capacitor_SMD:C_0402_1005Metric").
Added R9 (footprint "Resistor_SMD:R_0402_1005Metric").
Changed REF** reference designator to R9.
Changed R9 value from R_0402_1005Metric to 55K.
Updated R9 symbol association from  to /0cf2b8c0-70f6-4976-95f7-88ea6c192189/9ff4cea7-e9cf-46a1-9da8-9c5734c89337.
Updated R9 properties.
Connected R9 pin 1 to /PSU/PSU_EN.
Connected R9 pin 2 to Net-(R9-Pad2).
Connected C4 pin 2 to GND.
Added R10 (footprint "Resistor_SMD:R_0402_1005Metric").
Changed REF** reference designator to R10.
Changed R10 value from R_0402_1005Metric to 62K.
Updated R10 symbol association from  to /0cf2b8c0-70f6-4976-95f7-88ea6c192189/9f08719b-b284-4166-9d09-5cc443d36a77.
Updated R10 properties.
Connected R10 pin 1 to Net-(R10-Pad1).
Connected R10 pin 2 to GND.
Connected C4 pin 1 to +5V.
Added R11 (footprint "Resistor_SMD:R_0402_1005Metric").
Changed REF** reference designator to R11.
Changed R11 value from R_0402_1005Metric to 20K 1%.
Updated R11 symbol association from  to /0cf2b8c0-70f6-4976-95f7-88ea6c192189/00000000-0000-0000-0000-00005e540dfe.
Updated R11 properties.
Connected R11 pin 1 to Net-(C20-Pad1).
Connected R11 pin 2 to Net-(C21-Pad1).
Updated C4 properties.
Added R12 (footprint "Resistor_SMD:R_0402_1005Metric").
Changed REF** reference designator to R12.
Changed R12 value from R_0402_1005Metric to 12K 1%.
Updated R12 symbol association from  to /0cf2b8c0-70f6-4976-95f7-88ea6c192189/00000000-0000-0000-0000-00005e540df5.
Updated R12 properties.
Connected R12 pin 1 to Net-(C18-Pad1).
Connected R12 pin 2 to Net-(C22-Pad2).
Updated C4 symbol association from  to /93e7d8cf-e360-4b54-86be-d58fb9455bdf/35bb3e66-cd28-4912-a652-0e6c6f6d2357.
Added R13 (footprint "Resistor_SMD:R_0402_1005Metric").
Changed REF** reference designator to R13.
Changed R13 value from R_0402_1005Metric to 2.2K 1%.
Updated R13 symbol association from  to /0cf2b8c0-70f6-4976-95f7-88ea6c192189/00000000-0000-0000-0000-00005e540dfd.
Updated R13 properties.
Connected R13 pin 1 to Net-(C22-Pad2).
Connected R13 pin 2 to GND.
Changed C4 value from C_0402_1005Metric to 0u1 16V.
Added R14 (footprint "Resistor_SMD:R_0402_1005Metric").
Changed REF** reference designator to R14.
Changed R14 value from R_0402_1005Metric to 75K.
Updated R14 symbol association from  to /0cf2b8c0-70f6-4976-95f7-88ea6c192189/5e05eb7a-bdfc-4f67-a283-bd3dd446c9f4.
Updated R14 properties.
Connected R14 pin 1 to +3V3.
Connected R14 pin 2 to Net-(R14-Pad2).
Changed REF** reference designator to C4.
Added R15 (footprint "Resistor_SMD:R_0402_1005Metric").
Changed REF** reference designator to R15.
Changed R15 value from R_0402_1005Metric to 24K.
Updated R15 symbol association from  to /0cf2b8c0-70f6-4976-95f7-88ea6c192189/5d107841-540f-44b3-bbf4-7a1eecfe948e.
Updated R15 properties.
Connected R15 pin 1 to Net-(R14-Pad2).
Connected R15 pin 2 to GND.
Added C4 (footprint "Capacitor_SMD:C_0402_1005Metric").
Added R16 (footprint "Resistor_SMD:R_0402_1005Metric").
Changed REF** reference designator to R16.
Changed R16 value from R_0402_1005Metric to 10K.
Updated R16 symbol association from  to /1a1df624-ea52-444e-8eb0-2f13ef4aac9c/cb54f48b-b596-49c9-9a7f-14c49e5ee188.
Updated R16 properties.
Connected R16 pin 1 to +3V3.
Connected R16 pin 2 to /High Speed Interfaces/CAM0_SCL.
Connected C3 pin 2 to GND.
Added R17 (footprint "Resistor_SMD:R_0402_1005Metric").
Changed REF** reference designator to R17.
Changed R17 value from R_0402_1005Metric to 10K.
Updated R17 symbol association from  to /1a1df624-ea52-444e-8eb0-2f13ef4aac9c/cef1fb69-a64c-4671-9a19-9dc443fbf812.
Updated R17 properties.
Connected R17 pin 1 to +3V3.
Connected R17 pin 2 to /High Speed Interfaces/CAM0_SDA.
Connected C3 pin 1 to +5V.
Added R18 (footprint "Resistor_SMD:R_0402_1005Metric").
Changed REF** reference designator to R18.
Changed R18 value from R_0402_1005Metric to 10K.
Updated R18 symbol association from  to /1a1df624-ea52-444e-8eb0-2f13ef4aac9c/a4b641e4-3457-465b-802d-47977702d49c.
Updated R18 properties.
Connected R18 pin 1 to +3V3.
Connected R18 pin 2 to /High Speed Interfaces/CAM1_SCL.
Updated C3 properties.
Added R19 (footprint "Resistor_SMD:R_0402_1005Metric").
Changed REF** reference designator to R19.
Changed R19 value from R_0402_1005Metric to 10K.
Updated R19 symbol association from  to /1a1df624-ea52-444e-8eb0-2f13ef4aac9c/de5c7277-b4ff-4843-82a5-ee453cb00c3e.
Updated R19 properties.
Connected R19 pin 1 to +3V3.
Connected R19 pin 2 to /High Speed Interfaces/CAM1_SDA.
Updated C3 symbol association from  to /93e7d8cf-e360-4b54-86be-d58fb9455bdf/cb47f154-dea0-4a7d-97f1-dfb907c08eda.
Added R20 (footprint "Resistor_SMD:R_0402_1005Metric").
Changed REF** reference designator to R20.
Changed R20 value from R_0402_1005Metric to 12K.
Updated R20 symbol association from  to /b1d9abd2-56b2-476f-ba8d-e6505e2da0de/53af4974-5709-4a85-9230-3c9b996e6790.
Updated R20 properties.
Connected R20 pin 1 to +3V3_RPI.
Connected R20 pin 2 to Net-(R20-Pad2).
Changed C3 value from C_0402_1005Metric to 0u1 16V.
Added R21 (footprint "Resistor_SMD:R_0402_1005Metric").
Changed REF** reference designator to R21.
Changed R21 value from R_0402_1005Metric to 480.
Updated R21 symbol association from  to /93e7d8cf-e360-4b54-86be-d58fb9455bdf/3c52111a-c1bd-4eba-996f-1b1d7b2bc1e0.
Updated R21 properties.
Connected R21 pin 1 to Net-(D8-Pad1).
Connected R21 pin 2 to GND.
Changed REF** reference designator to C3.
Added SW1 (footprint "Button_Switch_SMD:Panasonic_EVQPUL_EVQPUC").
Changed REF** reference designator to SW1.
Changed SW1 value from Panasonic_EVQPUL_EVQPUC to SW_SPST.
Updated SW1 symbol association from  to /93e7d8cf-e360-4b54-86be-d58fb9455bdf/bbeeb38b-c746-4eb4-8cce-fc9483d32732.
Updated SW1 properties.
Connected SW1 pin 2 to GND.
Connected SW1 pin 2 to GND.
Connected SW1 pin 1 to Net-(SW1-Pad1).
Connected SW1 pin 1 to Net-(SW1-Pad1).
Added C3 (footprint "Capacitor_SMD:C_0402_1005Metric").
Added SW2 (footprint "Button_Switch_SMD:SW_SPDT_PCM12").
Changed REF** reference designator to SW2.
Changed SW2 value from SW_SPDT_PCM12 to SW_SPDT.
Updated SW2 symbol association from  to /057c2e08-823a-4406-b5ca-db4e8c27b194/9a689095-8a02-4c25-beb5-778005750bf5.
Updated SW2 properties.
Connected SW2 pin 1 to Net-(R5-Pad1).
Connected SW2 pin 2 to Net-(JP6-Pad1).
Connected SW2 pin 3 to GND.
Connected C2 pin 2 to GND.
Added SW3 (footprint "Button_Switch_SMD:SW_SPDT_PCM12").
Changed REF** reference designator to SW3.
Changed SW3 value from SW_SPDT_PCM12 to SW_SPDT.
Updated SW3 symbol association from  to /0cf2b8c0-70f6-4976-95f7-88ea6c192189/972158d3-e5b8-4d10-8557-0e5cc8dc5863.
Updated SW3 properties.
Connected SW3 pin 1 to +BATT.
Connected SW3 pin 2 to /PSU/PSU_EN.
Connected SW3 pin 3 to GND.
Connected C2 pin 1 to +5V.
Added TP4 (footprint "TestPoint:TestPoint_Pad_2.0x2.0mm").
Changed REF** reference designator to TP4.
Changed TP4 value from TestPoint_Pad_2.0x2.0mm to TestPoint.
Updated TP4 symbol association from  to /0cf2b8c0-70f6-4976-95f7-88ea6c192189/3fabcf40-eb07-4df1-8dba-07df8a40f7b8.
Updated TP4 properties.
Removed TP4 'exclude from BOM' fabrication attribute.
Connected TP4 pin 1 to Net-(C18-Pad1).
Updated C2 properties.
Added TP6 (footprint "TestPoint:TestPoint_Pad_2.0x2.0mm").
Changed REF** reference designator to TP6.
Changed TP6 value from TestPoint_Pad_2.0x2.0mm to TestPoint.
Updated TP6 symbol association from  to /0cf2b8c0-70f6-4976-95f7-88ea6c192189/00000000-0000-0000-0000-00005e5a1c5d.
Updated TP6 properties.
Removed TP6 'exclude from BOM' fabrication attribute.
Connected TP6 pin 1 to GND.
Updated C2 symbol association from  to /93e7d8cf-e360-4b54-86be-d58fb9455bdf/d10184b4-9280-4884-82aa-90d3f2b22364.
Added U1 (footprint "RPi_CM4IO:Raspberry-Pi-4-Compute-Module").
Changed REF** reference designator to U1.
Changed U1 value from Raspberry-Pi-4-Compute-Module to ComputeModule4-CM4.
Updated U1 symbol association from  to /93e7d8cf-e360-4b54-86be-d58fb9455bdf/5f93cc39-a1d9-4b17-bb56-467b966e2c1a.
Updated U1 properties.
Connected U1 pin 1 to GND.
Connected U1 pin 2 to GND.
Connected U1 pin 3 to /High Speed Interfaces/ETH.3_N.
Connected U1 pin 4 to /High Speed Interfaces/ETH.1_N.
Connected U1 pin 5 to /High Speed Interfaces/ETH.3_P.
Connected U1 pin 6 to /High Speed Interfaces/ETH.1_P.
Connected U1 pin 7 to GND.
Connected U1 pin 8 to GND.
Connected U1 pin 9 to /High Speed Interfaces/ETH.2_N.
Connected U1 pin 10 to /High Speed Interfaces/ETH.0_N.
Connected U1 pin 11 to /High Speed Interfaces/ETH.2_P.
Connected U1 pin 12 to /High Speed Interfaces/ETH.0_P.
Connected U1 pin 13 to GND.
Connected U1 pin 14 to GND.
Connected U1 pin 15 to unconnected-(U1-Pad15).
Connected U1 pin 16 to unconnected-(U1-Pad16).
Connected U1 pin 17 to /RPi_CM4/ETH_nLED2.
Connected U1 pin 18 to unconnected-(U1-Pad18).
Connected U1 pin 19 to /RPi_CM4/ETH_nLED1.
Connected U1 pin 20 to Net-(JP2-Pad2).
Connected U1 pin 21 to /RPi_CM4/RPI_nLED_ACT.
Connected U1 pin 22 to GND.
Connected U1 pin 23 to GND.
Connected U1 pin 24 to /RPi_CM4/SD_D_DAT2.
Connected U1 pin 25 to /RPi_CM4/SPI0.CLK.
Connected U1 pin 26 to /RPi_CM4/SPI0.MISO.
Connected U1 pin 27 to /RPi_CM4/SPI0.MOSI.
Connected U1 pin 28 to /RPi_CM4/UART1.RX.
Connected U1 pin 29 to /RPi_CM4/SPI0.CS2.
Connected U1 pin 30 to /RPi_CM4/GPIO_1.
Connected U1 pin 31 to /RPi_CM4/UART1.TX.
Connected U1 pin 32 to GND.
Connected U1 pin 33 to GND.
Connected U1 pin 34 to /RPi_CM4/GPIO_0.
Connected U1 pin 35 to /High Speed Interfaces/CAM0_SCL.
Connected U1 pin 36 to /High Speed Interfaces/CAM0_SDA.
Connected U1 pin 37 to /RPi_CM4/SPI1.CS1.
Connected U1 pin 38 to /RPi_CM4/SPI1.CLK.
Connected U1 pin 39 to /RPi_CM4/SPI1.CS0.
Connected U1 pin 40 to /RPi_CM4/SPI1.MISO.
Connected U1 pin 41 to /RPi_CM4/SD_D_DAT1.
Connected U1 pin 42 to GND.
Connected U1 pin 43 to GND.
Connected U1 pin 44 to /RPi_CM4/SPI1.MOSI.
Connected U1 pin 45 to /RPi_CM4/SD_D_DAT0.
Connected U1 pin 46 to /RPi_CM4/SD_D_CLK.
Connected U1 pin 47 to /RPi_CM4/SD_D_CMD.
Connected U1 pin 48 to /RPi_CM4/SD_D_DAT3.
Connected U1 pin 49 to /RPi_CM4/SPI0.CS0.
Connected U1 pin 50 to /RPi_CM4/SPI0.CS1.
Connected U1 pin 51 to /RPi_CM4/UART0.RX.
Connected U1 pin 52 to GND.
Connected U1 pin 53 to GND.
Connected U1 pin 54 to /RPi_CM4/RPI_SHTDWN.
Connected U1 pin 55 to /RPi_CM4/UART0.TX.
Connected U1 pin 56 to /RPi_CM4/I2C0.SCL.
Connected U1 pin 57 to /RPi_CM4/SD_O_CLK.
Connected U1 pin 58 to /RPi_CM4/I2C0.SDA.
Connected U1 pin 59 to GND.
Connected U1 pin 60 to GND.
Connected U1 pin 61 to /RPi_CM4/SD_O_DAT3.
Connected U1 pin 62 to /RPi_CM4/SD_O_CMD.
Connected U1 pin 63 to /RPi_CM4/SD_O_DAT0.
Connected U1 pin 64 to /RPi_CM4/SD_O_DAT5.
Connected U1 pin 65 to GND.
Connected U1 pin 66 to GND.
Connected U1 pin 67 to /RPi_CM4/SD_O_DAT1.
Connected U1 pin 68 to /RPi_CM4/SD_O_DAT4.
Connected U1 pin 69 to /RPi_CM4/SD_O_DAT2.
Connected U1 pin 70 to /RPi_CM4/SD_O_DAT7.
Connected U1 pin 71 to GND.
Connected U1 pin 72 to /RPi_CM4/SD_O_DAT6.
Connected U1 pin 73 to unconnected-(U1-Pad73).
Connected U1 pin 74 to GND.
Connected U1 pin 75 to /RPi_CM4/SD_O_PWRON.
Connected U1 pin 76 to unconnected-(U1-Pad76).
Connected U1 pin 77 to +5V.
Connected U1 pin 78 to +3V3_RPI.
Connected U1 pin 79 to +5V.
Connected U1 pin 80 to /High Speed Interfaces/CAM1_SCL.
Connected U1 pin 81 to +5V.
Connected U1 pin 82 to /High Speed Interfaces/CAM1_SDA.
Connected U1 pin 83 to +5V.
Connected U1 pin 84 to +3V3_RPI.
Connected U1 pin 85 to +5V.
Connected U1 pin 86 to +3V3_RPI.
Connected U1 pin 87 to +5V.
Connected U1 pin 88 to +1V8_RPI.
Connected U1 pin 89 to Net-(JP3-Pad2).
Connected U1 pin 90 to +1V8_RPI.
Connected U1 pin 91 to Net-(JP4-Pad2).
Connected U1 pin 92 to /RPi_CM4/RPI_RUN_PG.
Connected U1 pin 93 to Net-(JP1-Pad2).
Connected U1 pin 94 to unconnected-(U1-Pad94).
Connected U1 pin 95 to /RPi_CM4/RPI_nLED_PWR.
Connected U1 pin 96 to unconnected-(U1-Pad96).
Connected U1 pin 97 to /High Speed Interfaces/CAM_GPIO.
Connected U1 pin 98 to GND.
Connected U1 pin 99 to /RPi_CM4/RPI_GLOBL_EN.
Connected U1 pin 100 to unconnected-(U1-Pad100).
Connected U1 pin 101 to /RPi_CM4/USB_ID.
Connected U1 pin 102 to /AI/CORL_PCIE_NCLKREQ.
Connected U1 pin 103 to /RPi_CM4/USB_DN.
Connected U1 pin 104 to unconnected-(U1-Pad104).
Connected U1 pin 105 to /RPi_CM4/USB_DP.
Connected U1 pin 106 to unconnected-(U1-Pad106).
Connected U1 pin 107 to GND.
Connected U1 pin 108 to GND.
Connected U1 pin 109 to /AI/CORL_PCIE_NRST.
Connected U1 pin 110 to /AI/CORL_PCIE_CLK_P.
Connected U1 pin 111 to unconnected-(U1-Pad111).
Connected U1 pin 112 to /AI/CORL_PCIE_CLK_N.
Connected U1 pin 113 to GND.
Connected U1 pin 114 to GND.
Connected U1 pin 115 to /High Speed Interfaces/CAM1_MIPI.D0_N.
Connected U1 pin 116 to /AI/CORL_PCIE_TX_P.
Connected U1 pin 117 to /High Speed Interfaces/CAM1_MIPI.D0_P.
Connected U1 pin 118 to /AI/CORL_PCIE_TX_N.
Connected U1 pin 119 to GND.
Connected U1 pin 120 to GND.
Connected U1 pin 121 to /High Speed Interfaces/CAM1_MIPI.D1_N.
Connected U1 pin 122 to /AI/CORL_PCIE_RX_P.
Connected U1 pin 123 to /High Speed Interfaces/CAM1_MIPI.D1_P.
Connected U1 pin 124 to /AI/CORL_PCIE_RX_N.
Connected U1 pin 125 to GND.
Connected U1 pin 126 to GND.
Connected U1 pin 127 to /High Speed Interfaces/CAM1_MIPI.C_N.
Connected U1 pin 128 to /High Speed Interfaces/CAM0_MIPI.D0_N.
Connected U1 pin 129 to /High Speed Interfaces/CAM1_MIPI.C_P.
Connected U1 pin 130 to /High Speed Interfaces/CAM0_MIPI.D0_P.
Connected U1 pin 131 to GND.
Connected U1 pin 132 to GND.
Connected U1 pin 133 to /High Speed Interfaces/CAM1_MIPI.D2_N.
Connected U1 pin 134 to /High Speed Interfaces/CAM0_MIPI.D1_N.
Connected U1 pin 135 to /High Speed Interfaces/CAM1_MIPI.D2_P.
Connected U1 pin 136 to /High Speed Interfaces/CAM0_MIPI.D1_P.
Connected U1 pin 137 to GND.
Connected U1 pin 138 to GND.
Connected U1 pin 139 to /High Speed Interfaces/CAM1_MIPI.D3_N.
Connected U1 pin 140 to /High Speed Interfaces/CAM0_MIPI.C_N.
Connected U1 pin 141 to /High Speed Interfaces/CAM1_MIPI.D3_P.
Connected U1 pin 142 to /High Speed Interfaces/CAM0_MIPI.C_P.
Connected U1 pin 143 to unconnected-(U1-Pad143).
Connected U1 pin 144 to GND.
Connected U1 pin 145 to unconnected-(U1-Pad145).
Connected U1 pin 146 to unconnected-(U1-Pad146).
Connected U1 pin 147 to unconnected-(U1-Pad147).
Connected U1 pin 148 to unconnected-(U1-Pad148).
Connected U1 pin 149 to unconnected-(U1-Pad149).
Connected U1 pin 150 to GND.
Connected U1 pin 151 to unconnected-(U1-Pad151).
Connected U1 pin 152 to unconnected-(U1-Pad152).
Connected U1 pin 153 to unconnected-(U1-Pad153).
Connected U1 pin 154 to unconnected-(U1-Pad154).
Connected U1 pin 155 to GND.
Connected U1 pin 156 to GND.
Connected U1 pin 157 to unconnected-(U1-Pad157).
Connected U1 pin 158 to unconnected-(U1-Pad158).
Connected U1 pin 159 to unconnected-(U1-Pad159).
Connected U1 pin 160 to unconnected-(U1-Pad160).
Connected U1 pin 161 to GND.
Connected U1 pin 162 to GND.
Connected U1 pin 163 to unconnected-(U1-Pad163).
Connected U1 pin 164 to unconnected-(U1-Pad164).
Connected U1 pin 165 to unconnected-(U1-Pad165).
Connected U1 pin 166 to unconnected-(U1-Pad166).
Connected U1 pin 167 to GND.
Connected U1 pin 168 to GND.
Connected U1 pin 169 to unconnected-(U1-Pad169).
Connected U1 pin 170 to unconnected-(U1-Pad170).
Connected U1 pin 171 to unconnected-(U1-Pad171).
Connected U1 pin 172 to unconnected-(U1-Pad172).
Connected U1 pin 173 to GND.
Connected U1 pin 174 to GND.
Connected U1 pin 175 to unconnected-(U1-Pad175).
Connected U1 pin 176 to unconnected-(U1-Pad176).
Connected U1 pin 177 to unconnected-(U1-Pad177).
Connected U1 pin 178 to unconnected-(U1-Pad178).
Connected U1 pin 179 to GND.
Connected U1 pin 180 to GND.
Connected U1 pin 181 to unconnected-(U1-Pad181).
Connected U1 pin 182 to unconnected-(U1-Pad182).
Connected U1 pin 183 to unconnected-(U1-Pad183).
Connected U1 pin 184 to unconnected-(U1-Pad184).
Connected U1 pin 185 to GND.
Connected U1 pin 186 to GND.
Connected U1 pin 187 to unconnected-(U1-Pad187).
Connected U1 pin 188 to unconnected-(U1-Pad188).
Connected U1 pin 189 to unconnected-(U1-Pad189).
Connected U1 pin 190 to unconnected-(U1-Pad190).
Connected U1 pin 191 to GND.
Connected U1 pin 192 to GND.
Connected U1 pin 193 to unconnected-(U1-Pad193).
Connected U1 pin 194 to unconnected-(U1-Pad194).
Connected U1 pin 195 to unconnected-(U1-Pad195).
Connected U1 pin 196 to unconnected-(U1-Pad196).
Connected U1 pin 197 to GND.
Connected U1 pin 198 to GND.
Connected U1 pin 199 to unconnected-(U1-Pad199).
Connected U1 pin 200 to unconnected-(U1-Pad200).
Changed C2 value from C_0402_1005Metric to 0u1 16V.
Added U2 (footprint "Package_SO:SOIC-8W_5.3x5.3mm_P1.27mm").
Changed REF** reference designator to U2.
Changed U2 value from SOIC-8W_5.3x5.3mm_P1.27mm to ATtiny85V-10S.
Updated U2 symbol association from  to /93e7d8cf-e360-4b54-86be-d58fb9455bdf/de31e5cd-adec-4cc4-b5dc-4ca47516a007.
Updated U2 properties.
Connected U2 pin 1 to unconnected-(U2-Pad1).
Connected U2 pin 2 to /RPi_CM4/RPI_SHTDWN.
Connected U2 pin 3 to Net-(D8-Pad2).
Connected U2 pin 4 to GND.
Connected U2 pin 5 to Net-(SW1-Pad1).
Connected U2 pin 6 to /RPi_CM4/RPI_RUN_PG.
Connected U2 pin 7 to Net-(Q1-Pad1).
Connected U2 pin 8 to +3V3_RPI.
Changed REF** reference designator to C2.
Added U3 (footprint "Package_TO_SOT_SMD:SOT-353_SC-70-5").
Changed REF** reference designator to U3.
Changed U3 value from SOT-353_SC-70-5 to 74LVC1G07.
Updated U3 symbol association from  to /93e7d8cf-e360-4b54-86be-d58fb9455bdf/f3bc1303-8982-41ec-8ecc-cedb5185de67.
Updated U3 properties.
Connected U3 pin 3 to GND.
Connected U3 pin 2 to /RPi_CM4/RPI_nLED_PWR.
Connected U3 pin 4 to Net-(R4-Pad2).
Connected U3 pin 5 to +3V3_RPI.
Added C2 (footprint "Capacitor_SMD:C_0402_1005Metric").
Added U4 (footprint "AI_Coral:G313-06329-00").
Changed REF** reference designator to U4.
Changed U4 value from MODULE_G313-06329-00 to G313-06329-00.
Updated U4 symbol association from  to /c7aadd96-de8c-4974-aee8-6d5527743de5/e9001580-821b-436a-9094-2a99188a54fe.
Updated U4 properties.
Connected U4 pin 45 to GND.
Connected U4 pin 1 to GND.
Connected U4 pin 6 to GND.
Connected U4 pin 5 to /AI/CORL_PCIE_TX_P.
Connected U4 pin 4 to /AI/CORL_PCIE_TX_N.
Connected U4 pin 3 to GND.
Connected U4 pin 2 to GND.
Connected U4 pin 64 to +3V3.
Connected U4 pin 20 to GND.
Connected U4 pin 101 to GND.
Connected U4 pin 100 to GND.
Connected U4 pin 99 to GND.
Connected U4 pin 98 to GND.
Connected U4 pin 97 to GND.
Connected U4 pin 102 to GND.
Connected U4 pin 103 to GND.
Connected U4 pin 104 to GND.
Connected U4 pin 93 to GND.
Connected U4 pin 92 to GND.
Connected U4 pin 91 to GND.
Connected U4 pin 90 to GND.
Connected U4 pin 89 to GND.
Connected U4 pin 94 to GND.
Connected U4 pin 95 to GND.
Connected U4 pin 96 to GND.
Connected U4 pin 109 to GND.
Connected U4 pin 108 to GND.
Connected U4 pin 107 to GND.
Connected U4 pin 106 to GND.
Connected U4 pin 105 to GND.
Connected U4 pin 110 to GND.
Connected U4 pin 111 to GND.
Connected U4 pin 112 to GND.
Connected U4 pin 117 to GND.
Connected U4 pin 116 to GND.
Connected U4 pin 115 to GND.
Connected U4 pin 114 to GND.
Connected U4 pin 113 to GND.
Connected U4 pin 118 to GND.
Connected U4 pin 119 to GND.
Connected U4 pin 120 to GND.
Connected U4 pin 7 to /AI/CORL_PCIE_RX_P.
Connected U4 pin 8 to /AI/CORL_PCIE_RX_N.
Connected U4 pin 9 to GND.
Connected U4 pin 10 to /AI/CORL_PCIE_CLK_N.
Connected U4 pin 11 to /AI/CORL_PCIE_CLK_P.
Connected U4 pin 12 to GND.
Connected U4 pin 13 to unconnected-(U4-Pad13).
Connected U4 pin 14 to unconnected-(U4-Pad14).
Connected U4 pin 15 to GND.
Connected U4 pin 16 to GND.
Connected U4 pin 17 to GND.
Connected U4 pin 18 to GND.
Connected U4 pin 19 to GND.
Connected U4 pin 21 to GND.
Connected U4 pin 22 to GND.
Connected U4 pin 23 to GND.
Connected U4 pin 24 to GND.
Connected U4 pin 25 to GND.
Connected U4 pin 26 to GND.
Connected U4 pin 27 to GND.
Connected U4 pin 28 to GND.
Connected U4 pin 29 to GND.
Connected U4 pin 30 to GND.
Connected U4 pin 31 to GND.
Connected U4 pin 32 to GND.
Connected U4 pin 33 to GND.
Connected U4 pin 34 to GND.
Connected U4 pin 35 to GND.
Connected U4 pin 36 to GND.
Connected U4 pin 37 to unconnected-(U4-Pad37).
Connected U4 pin 38 to GND.
Connected U4 pin 39 to GND.
Connected U4 pin 40 to GND.
Connected U4 pin 41 to GND.
Connected U4 pin 42 to GND.
Connected U4 pin 43 to GND.
Connected U4 pin 44 to GND.
Connected U4 pin 46 to GND.
Connected U4 pin 47 to GND.
Connected U4 pin 48 to GND.
Connected U4 pin 49 to unconnected-(U4-Pad49).
Connected U4 pin 50 to unconnected-(U4-Pad50).
Connected U4 pin 51 to GND.
Connected U4 pin 52 to unconnected-(U4-Pad52).
Connected U4 pin 53 to unconnected-(U4-Pad53).
Connected U4 pin 54 to +1V8_RPI.
Connected U4 pin 55 to GND.
Connected U4 pin 56 to +3V3.
Connected U4 pin 57 to +3V3.
Connected U4 pin 58 to +3V3.
Connected U4 pin 59 to +3V3.
Connected U4 pin 60 to +3V3.
Connected U4 pin 61 to +3V3.
Connected U4 pin 62 to +3V3.
Connected U4 pin 63 to +3V3.
Connected U4 pin 65 to +3V3.
Connected U4 pin 66 to +3V3.
Connected U4 pin 67 to +3V3.
Connected U4 pin 68 to GND.
Connected U4 pin 69 to GND.
Connected U4 pin 70 to GND.
Connected U4 pin 71 to GND.
Connected U4 pin 72 to GND.
Connected U4 pin 73 to GND.
Connected U4 pin 74 to GND.
Connected U4 pin 75 to GND.
Connected U4 pin 76 to /AI/CORL_PCIE_NRST.
Connected U4 pin 77 to unconnected-(U4-Pad77).
Connected U4 pin 78 to /AI/CORL_PCIE_NCLKREQ.
Connected U4 pin 79 to GND.
Connected U4 pin 80 to GND.
Connected U4 pin 81 to GND.
Connected U4 pin 82 to unconnected-(U4-Pad82).
Connected U4 pin 83 to unconnected-(U4-Pad83).
Connected U4 pin 84 to unconnected-(U4-Pad84).
Connected U4 pin 85 to unconnected-(U4-Pad85).
Connected U4 pin 86 to GND.
Connected U4 pin 87 to GND.
Connected U4 pin 88 to GND.
Connected C1 pin 2 to GND.
Added U5 (footprint "Package_TO_SOT_SMD:Texas_DRT-3").
Changed REF** reference designator to U5.
Changed U5 value from Texas_DRT-3 to TPD2EUSB30.
Updated U5 symbol association from  to /057c2e08-823a-4406-b5ca-db4e8c27b194/74eedc7e-bd2f-4fe5-b047-4d08683c74bc.
Updated U5 properties.
Connected U5 pin 1 to /RPi_CM4/USB_DP.
Connected U5 pin 2 to /RPi_CM4/USB_DN.
Connected U5 pin 3 to GND.
Connected C1 pin 1 to +5V.
Added U6 (footprint "Package_DFN_QFN:Texas_X2QFN-12_1.6x1.6mm_P0.4mm").
Changed REF** reference designator to U6.
Changed U6 value from Texas_X2QFN-12_1.6x1.6mm_P0.4mm to TUSB321.
Updated U6 symbol association from  to /057c2e08-823a-4406-b5ca-db4e8c27b194/b447008e-382d-4ba3-afe9-f86c2482b33e.
Updated U6 properties.
Connected U6 pin 1 to Net-(J2-PadA5).
Connected U6 pin 2 to Net-(J2-PadB5).
Connected U6 pin 3 to Net-(R7-Pad2).
Connected U6 pin 4 to Net-(JP6-Pad2).
Connected U6 pin 5 to Net-(R6-Pad1).
Connected U6 pin 6 to /USB/VUSB_FAULT.
Connected U6 pin 7 to unconnected-(U6-Pad7).
Connected U6 pin 8 to unconnected-(U6-Pad8).
Connected U6 pin 9 to /RPi_CM4/USB_ID.
Connected U6 pin 10 to GND.
Connected U6 pin 11 to unconnected-(U6-Pad11).
Connected U6 pin 12 to +5V.
Updated C1 properties.
Connected U16 pin 9 to GND.
Updated C1 symbol association from  to /93e7d8cf-e360-4b54-86be-d58fb9455bdf/f1a7809f-8dd0-490d-9a21-230b15cd185e.
Added U8 (footprint "Package_SON:USON-10_2.5x1.0mm_P0.5mm").
Changed REF** reference designator to U8.
Changed U8 value from USON-10_2.5x1.0mm_P0.5mm to TPD4EUSB30.
Updated U8 symbol association from  to /1a1df624-ea52-444e-8eb0-2f13ef4aac9c/608f2802-a7ad-4c10-99a0-95f4d98b6393.
Updated U8 properties.
Connected U8 pin 1 to /High Speed Interfaces/ETH.0_P.
Connected U8 pin 2 to /High Speed Interfaces/ETH.0_N.
Connected U8 pin 3 to GND.
Connected U8 pin 4 to /High Speed Interfaces/ETH.1_P.
Connected U8 pin 5 to /High Speed Interfaces/ETH_1_N.
Connected U8 pin 9 to unconnected-(U8-Pad9).
Connected U8 pin 6 to unconnected-(U8-Pad6).
Connected U8 pin 7 to unconnected-(U8-Pad7).
Connected U8 pin 10 to unconnected-(U8-Pad10).
Connected U8 pin 8 to GND.
Changed C1 value from C_0402_1005Metric to 0u1 16V.
Added U9 (footprint "Package_SON:USON-10_2.5x1.0mm_P0.5mm").
Changed REF** reference designator to U9.
Changed U9 value from USON-10_2.5x1.0mm_P0.5mm to TPD4EUSB30.
Updated U9 symbol association from  to /1a1df624-ea52-444e-8eb0-2f13ef4aac9c/33ad990f-981f-4585-952d-df5c7496ae02.
Updated U9 properties.
Connected U9 pin 1 to /High Speed Interfaces/ETH.2_P.
Connected U9 pin 2 to /High Speed Interfaces/ETH.2_N.
Connected U9 pin 3 to GND.
Connected U9 pin 4 to /High Speed Interfaces/ETH.3_N.
Connected U9 pin 5 to /High Speed Interfaces/ETH.3_P.
Connected U9 pin 9 to unconnected-(U9-Pad9).
Connected U9 pin 6 to unconnected-(U9-Pad6).
Connected U9 pin 7 to unconnected-(U9-Pad7).
Connected U9 pin 10 to unconnected-(U9-Pad10).
Connected U9 pin 8 to GND.
Changed REF** reference designator to C1.
Added U10 (footprint "Package_TO_SOT_SMD:SOT-23-5").
Changed REF** reference designator to U10.
Changed U10 value from SOT-23-5 to RT9742GGJ5.
Updated U10 symbol association from  to /b1d9abd2-56b2-476f-ba8d-e6505e2da0de/0fc79c96-3f91-44c7-8e10-a6e236b60086.
Updated U10 properties.
Connected U10 pin 1 to /SD Card/SD_PWR.
Connected U10 pin 2 to GND.
Connected U10 pin 3 to unconnected-(U10-Pad3).
Connected U10 pin 4 to Net-(R20-Pad2).
Connected U10 pin 5 to +3V3_RPI.
Added C1 (footprint "Capacitor_SMD:C_0402_1005Metric").
Added U16 (footprint "Package_SO:SOIC-8-1EP_3.9x4.9mm_P1.27mm_EP2.95x4.9mm_Mask2.71x3.4mm_ThermalVias").
Changed REF** reference designator to U16.
Changed U16 value from SOIC-8-1EP_3.9x4.9mm_P1.27mm_EP2.95x4.9mm_Mask2.71x3.4mm_ThermalVias to AP64501SP-13.
Updated U16 symbol association from  to /0cf2b8c0-70f6-4976-95f7-88ea6c192189/00000000-0000-0000-0000-00005e540df9.
Updated U16 properties.
Connected U16 pin 1 to Net-(C15-Pad2).
Connected U16 pin 2 to +BATT.
Connected U16 pin 3 to /PSU/PSU_EN.
Connected U16 pin 4 to Net-(C17-Pad1).
Connected U16 pin 5 to Net-(C22-Pad2).
Connected U16 pin 6 to Net-(C20-Pad1).
Connected U16 pin 7 to GND.
Connected U16 pin 8 to Net-(L1-Pad1).
Connected U16 pin 9 to GND.
Connected U16 pin 9 to GND.
Connected U16 pin 9 to GND.
Connected U16 pin 9 to GND.
Connected U16 pin 9 to GND.
Connected U16 pin 9 to GND.
Connected U16 pin 9 to GND.
Connected U16 pin 9 to GND.
Error: 
Error: 

Info: Total warnings: 0, errors: 2.

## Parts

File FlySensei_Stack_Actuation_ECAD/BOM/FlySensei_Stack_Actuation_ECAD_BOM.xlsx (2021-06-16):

Item # | Designator | Qty | Manufacturer | Mfg Part # | Description / Value | Package/Footprint | Type | Your Instructions / Notes
1 | BL0, BL1, BL2, BL3, BL4, BL5, BL6, BL7, S0, S1, S2, S3, S4, S5, S6, S7 | 16 | JST | SM03B-GHS-TB(LF)(SN) | CONN HEADER SMD R/A 3POS 1.25MM | JST_GH_SM03B-GHS-TB_1x03-1MP_P1.25mm_Horizontal | SMD
2 | C1 | 1 | Murata Electronics | GRT188C8YA105KE13D | CAP CER 1UF 35V X6S 0603 | 0603 | SMD
3 | C2, C3, C8, C9, C31, C33 | 6 | Murata Electronics | GRM188R61E106KA73D | CAP CER 10UF 25V X5R 0603 | 0603 | SMD
4 | C4, C5, C10, C11, C18, C19, C20, C21, C26, C27, C28, C29 | 12 | Taiyo Yuden | TMK105AC6105MV-F | CAP CER 1UF 25V X6S 0402 | 0402 | SMD
5 | C6, C7, C12, C13, C14, C15, C16, C17, C22, C23, C24, C25 | 12 | Murata Electronics | GRM155R71E104ME14D | CAP CER 0.1UF 25V X7R 0402 | 0402 | SMD
6 | C30 | 1 | Panasonic | EEF-CX0J101R | CAP ALUM POLY 100UF 20% 6.3V SMD | 2917 | SMD
7 | C32, C34 | 2 | Murata Electronics | GRM188R61A226ME15D | CAP CER 22UF 10V X5R 0603 | 0603 | SMD
8 | C35 | 1 | Murata Electronics | GCM155R71H102KA37D | CAP CER 1000PF 50V X7R 0402 | 0402 | SMD
9 | D1 | 1 | Würth Elektronik | 150060RS75000 | LED RED CLEAR 0603 SMD | 0603 | SMD
10 | J1, J3 | 2 | Samtec Inc. | FTSH-120-01-F-DV | CONN HEADER SMD 40POS 1.27MM | PinHeader_2x20_P1.27mm_Vertical_SMD | SMD
11 | J2, J4 | 2 | Samtec Inc. | CLP-120-02-L-D | CONN RCPT 40POS 0.05 GOLD SMD | PinHeader_2x20_P1.27mm_Vertical_SMD | SMD
12 | J5 | 1 | JST | S2B-PH-SM4-TB(LF)(SN) | CONN HEADER SMD R/A 2POS 2MM | JST_PH_S2B-PH-SM4-TB_1x02-1MP_P2.00mm_Horizontal | SMD
13 | M0, M1, M2, M3 | 4 | JST | SM02B-GHS-TB(LF)(SN) | CONN HEADER SMD R/A 2POS 1.25MM | JST_GH_SM02B-GHS-TB_1x02-1MP_P1.25mm_Horizontal | SMD
14 | R1, R2, R3, R4, R5, R6, R7, R17, R18 | 9 | Panasonic Electronic Components | ERA-2ARB103X | RES SMD 10K OHM 0.1% 1/16W 0402 | 0402 | SMD
15 | R8 | 1 | Panasonic Electronic Components | ERA-2AED271X | RES SMD 270 OHM 0.5% 1/16W 0402 | 0402 | SMD
16 | R9, R10 | 2 | Yageo | RT0402BRD0754K9L | RES SMD 54.9KOHM 0.1% 1/16W 0402 | 0402 | SMD
17 | R11 | 1 | Yageo | RT0402BRD0762KL | RES SMD 62K OHM 0.1% 1/16W 0402 | 0402 | SMD
18 | R12 | 1 | Yageo | RT0402BRE0773K2L | RES SMD 73.2KOHM 0.1% 1/16W 0402 | 0402 | SMD
19 | R13 | 1 | Panasonic Electronic Components | ERA-2AEB753X | RES SMD 75K OHM 0.1% 1/16W 0402 | 0402 | SMD
20 | R14 | 1 | Panasonic Electronic Components | ERA-2AEB243X | RES SMD 24K OHM 0.1% 1/16W 0402 | 0402 | SMD
21 | R15 | 1 | Panasonic Electronic Components | ERA-2AEB104X | RES SMD 100K OHM 0.1% 1/16W 0402 | 0402 | SMD
22 | R16 | 1 | Panasonic Electronic Components | ERA-2AEB753X | RES SMD 75K OHM 0.1% 1/16W 0402 | 0402 | SMD
23 | SW1, SW2 | 2 | C&K | PCM12SMTR | SWITCH SLIDE SPDT 300MA 6V | PCM12 | SMD
24 | U1 | 1 | NXP | PCA9685PW,118 | IC LED DRVR LIN DIM 25MA 28HVQFN | 28-HVQFN | SMD
25 | U2, U3, U4, U5 | 4 | Texas Instruments | DRV8835DSSR | IC MTR DRVR BIPOLAR 2-7V 12WSON | 12-WSON | SMD
26 | U6, U7 | 2 | Monolithic Power Systems Inc. | MPM3610GQV-P | DC DC CONVERTER 0.8-18.48V | 20-QFN | SMD
27 | U8 | 1 | Maxim Integrated | MAX17059G+ | IC BATT FUEL LI-ION 2C 8TDFN | 8-TDFN | SMD
28 | U9, U10 | 2 | Texas Instruments | TS5A3159ADCKR | IC SWITCH SPDT SC70-6 | SC-70-6 | SMD

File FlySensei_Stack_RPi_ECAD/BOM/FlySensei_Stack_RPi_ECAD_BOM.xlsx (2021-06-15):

Item # | Designator | Qty | Manufacturer | Mfg Part # | Description / Value | Package/Footprint | Type | Your Instructions / Notes
1 | C1, C2, C3, C4 | 4 | Murata Electronics | GRT155R71C104KE01J | CAP CER 0.1UF 16V X7R 0402 | 0402 | SMD
2 | C5, C6, C7, C8, C9, C10 | 6 | Murata Electronics | GRT155R71C104KE01J | CAP CER 0.1UF 16V X7R 0402 | 0603 | SMD
3 | C11, C19 | 2 | Samsung Electro-Mechanics | CL10A226MO7JZNC | CAP CER 22UF 16V X5R 0603 | 0603 | SMD
4 | C12 | 1 | Murata Electronics | GRT188C8YA105KE13D | CAP CER 1UF 35V X6S 0603 | 0603 | SMD
5 | C13, C14 | 2 | Murata Electronics | GRM21BC8YA106ME11L | CAP CER 10UF 35V X6S 0805 | 0805 | SMD
6 | C15, C17 | 2 | Taiyo Yuden | EMK105B7104KV-F | CAP CER 0.1UF 16V X7R 0402 | 0402 | SMD
7 | C16 | 1 | Taiyo Yuden | GMK107AB7105KAHT | CAP CER 1UF 35V X7R 0603 | 0603 | SMD
8 | C18 | 1 | Panasonic | EEF-CX0J101R | CAP ALUM POLY 100UF 20% 6.3V SMD | 2917 | SMD
9 | C20, C22 | 2 | Murata Electronics | GRM1555C1H102FA01J | CAP CER 1000PF 50V C0G/NP0 0402 | 0402 | SMD
10 | C21 | 1 | Murata Electronics | GCM155R71H122KA37D | CAP CER 1200PF 50V X7R 0402 | 0402 | SMD
11 | C23, C24, C25, C26 | 4 | Murata Electronics | GRM21BZ71A226ME15L | CAP CER 22UF 10V X7R 0805 | 0805 | SMD
13 | C27 | 1 | Murata Electronics | GRM21BR71A106KA73K | CAP CER 10UF 10V X7R 0805 | 0805 | SMD
14 | D1, D2 | 2 | Würth Elektronik | 150060VS75000 | LED GREEN CLEAR 0603 SMD | 0603 | SMD
15 | D3 | 1 | Würth Elektronik | 150060AS75000 | WL-SMCW SMT MONO-COLOR CHIP LED | 0603 | SMD
16 | D4 | 1 | Würth Elektronik | 150060RS75000 | LED RED CLEAR 0603 SMD | 0603 | SMD
17 | D5, D6, D7 | 3 | Diodes Incorporated | B330B-13-F | DIODE SCHOTTKY 30V 3A SMB | SMB | SMD
18 | D8 | 1 | Würth Elektronik | 150060BS75000 | LED BLUE CLEAR 0603 SMD | 0603 | SMD
21 | J2 | 1 | GCT | USB4105-GF-A | CONN RCP USB2.0 TYP C 24P SMD RA | USB-C-Recepticle | SMD
22 | J3, J5 | 2 | Samtec Inc. | FTSH-120-01-F-DV | CONN HEADER SMD 40POS 1.27MM | PinHeader_2x20_P1.27mm_Vertical_SMD | SMD
23 | J4, J6 | 2 | Samtec Inc. | CLP-120-02-L-D | CONN RCPT 40POS 0.05 GOLD SMD | PinHeader_2x20_P1.27mm_Vertical_SMD | SMD
24 | J7, J8 | 2 | Hirose Electric Co Ltd | FH12-22S-0.5SH | CONN FFC BOTTOM 22POS 0.50MM R/A | Hirose_FH12-22S-0.5SH_1x22-1MP_P0.50mm_Horizontal | SMD
25 | J9 | 1 | Hirose Electric Co Ltd | FH12-14S-0.5SH | CONN FFC BOTTOM 14POS 0.50MM R/A | Hirose_FH12-14S-0.5SH_1x14-1MP_P0.50mm_Horizontal | SMD
26 | J10 | 1 | Molex | 5033981892 | MICRO SD PUSH/PUSH SMALL 8C | SDCARD_MOLEX_503398-1892 | SMD
27 | L1 | 1 | Bourns Inc. | SRN6045TA-3R3Y | FIXED IND 3.3UH 5A 21 MOHM SMD | L_Bourns_SRN6045TA | SMD
28 | Q1 | 1 | Micro Commercial Co | SI2302-TP | MOSFET N-CH 20V 3A SOT-23 | SOT-23 | SMD
29 | R1, R2, R3, R4 | 4 | Panasonic Electronic Components | ERA-2AED271X | RES SMD 270 OHM 0.5% 1/16W 0402 | 0402 | SMD
30 | R5 | 1 | Panasonic | ERA-2AED472X | RES SMD 4.7K OHM 0.5% 1/16W 0402 | 0402 | SMD
31 | R6 | 1 | Panasonic Electronic Components | ERJ-2RKF9093X | RES SMD 909K OHM 1% 1/10W 0402 | 0402 | SMD
32 | R7 | 1 | Yageo | RT0402BRD0751KL | RES SMD 51K OHM 0.1% 1/16W 0402 | 0402 | SMD
33 | R8 | 1 | Yageo | RC0402FR-0710RL | RES SMD 10 OHM 1% 1/16W 0402 | 0402 | SMD
34 | R9 | 1 | Yageo | RT0402BRD0754K9L | RES SMD 54.9KOHM 0.1% 1/16W 0402 | 0402 | SMD
35 | R10 | 1 | Yageo | RT0402BRD0762KL | RES SMD 62K OHM 0.1% 1/16W 0402 | 0402 | SMD
36 | R11 | 1 | KOA Speer Electronics, Inc. | RK73H1ETTP2002F | RES 20K OHM 1% 1/10W 0402 | 0402 | SMD
37 | R12 | 1 | Rohm Semiconductor | MCR01MZPF1202 | RES SMD 12K OHM 1% 1/16W 0402 | 0402 | SMD
38 | R13 | 1 | Yageo | RC0402FR-072K2L | RES SMD 2.2K OHM 1% 1/16W 0402 | 0402 | SMD
39 | R14 | 1 | KOA Speer Electronics, Inc. | RN73R1ETTP7502B25 | RES 75K OHM 0.1% 1/16W 0402 | 0402 | SMD
40 | R15 | 1 | Panasonic Electronic Components | ERA-2AEB243X | RES SMD 24K OHM 0.1% 1/16W 0402 | 0402 | SMD
41 | R16, R17, R18, R19 | 4 | Panasonic Electronic Components | ERA-2ARB103X | RES SMD 10K OHM 0.1% 1/16W 0402 | 0402 | SMD
42 | R20 | 1 | Yageo | RC0402FR-0712KL | RES SMD 12K OHM 1% 1/16W 0402 | 0402 | SMD
43 | R21 | 1 | Panasonic Electronic Components | ERA-2AEB4870X | RES SMD 487 OHM 0.1% 1/16W 0402 | 0402 | SMD
44 | SW1 | 1 | Panasonic Electronic Components | EVQ-PUL02K | SWITCH TACTILE SPST-NO 0.05A 12V | Panasonic_EVQPUL_EVQPUC | SMD
45 | SW2, SW3 | 2 | C&K | PCM12SMTR | SWITCH SLIDE SPDT 300MA 6V | PCM12 | SMD
46 | U1 | 1 | Hirose Electric Co Ltd | DF40C-100DS-0.4V(51) | CONN RCPT 100POS SMD GOLD | Hirose_DF40C-100DS-0.4V_P0.5mm_SMD | SMD | There are 2 connectors in the same footprint.
47 | U2 | 1 | Microchip Technology | ATTINY85V-10SU | IC MCU 8BIT 8KB FLASH 8SOIC | 8-SOIC | SMD
48 | U3 | 1 | Texas Instruments | SN74LVC1G07DCK3 | IC BUFFER NON-INVERT 5.5V SC70-5 | SC-70-5 | SMD
49 | U4 | 1 | Google Coral | G313-06329-00 | IC ACCELERATOR SPECIALIZED LGA | LGA | SMD
50 | U5 | 1 | Texas Instruments | TPD2EUSB30DRTR | TVS DIODE 5.5VWM 8VC SOT9X3 | SOT | SMD
51 | U6 | 1 | Texas Instruments | TUSB321AIRWBR | IC INTERFACE SPECIALIZED 12X2QFN | QFN | SMD
52 | U7 | 1 | Monolithic Power Systems Inc. | MPM3610GQV-P | DC DC CONVERTER 0.8-18.48V | LGA | SMD
53 | U8, U9 | 2 | Texas Instruments | TPD4EUSB30DQAR | TVS DIODE 5.5VWM 8VC 10USON | 10USON | SMD
54 | U10 | 1 | Richtek USA Inc. | RT9742GGJ5 | IC PWR SWTCH N-CHAN 1:1 TSOT23-5 | TSOT23-5 | SMD
55 | U16 | 1 | Diodes Incorporated | AP64501SP-13 | DCDC CONV HV BUCK SO-8EP | SOIC8 | SMD

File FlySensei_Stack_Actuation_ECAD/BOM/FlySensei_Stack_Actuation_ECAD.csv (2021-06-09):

Source: | /Users/joseph/Onedrive_JPM/OneDrive - George Mason University/Classwork/Research/Project_BlimpSquad/PCB/FlySensei_Stack_ECAD/FlySensei_Stack_Actuation_ECAD/FlySensei_Stack_Actuation_ECAD.kicad_sch
Date: | Wednesday, June 09, 2021 at 11:17:35 AM
Tool: | Eeschema (5.99.0-10928-g75ce97e260)
Generator: | /Applications/KiCad/KiCad.app/Contents/SharedSupport/plugins/bom_csv_grouped_by_value.py
Component Count: | 102
Individual Components:
Item | Qty | Reference(s) | Value | LibPart | Footprint | Datasheet
 |  | BL0 | Conn_01x03 | Connector_Generic:Conn_01x03 | Connector_JST:JST_GH_SM03B-GHS-TB_1x03-1MP_P1.25mm_Horizontal | ~
 |  | BL1 | Conn_01x03 | Connector_Generic:Conn_01x03 | Connector_JST:JST_GH_SM03B-GHS-TB_1x03-1MP_P1.25mm_Horizontal | ~
 |  | BL2 | Conn_01x03 | Connector_Generic:Conn_01x03 | Connector_JST:JST_GH_SM03B-GHS-TB_1x03-1MP_P1.25mm_Horizontal | ~
 |  | BL3 | Conn_01x03 | Connector_Generic:Conn_01x03 | Connector_JST:JST_GH_SM03B-GHS-TB_1x03-1MP_P1.25mm_Horizontal | ~
 |  | BL4 | Conn_01x03 | Connector_Generic:Conn_01x03 | Connector_JST:JST_GH_SM03B-GHS-TB_1x03-1MP_P1.25mm_Horizontal | ~
 |  | BL5 | Conn_01x03 | Connector_Generic:Conn_01x03 | Connector_JST:JST_GH_SM03B-GHS-TB_1x03-1MP_P1.25mm_Horizontal | ~
 |  | BL6 | Conn_01x03 | Connector_Generic:Conn_01x03 | Connector_JST:JST_GH_SM03B-GHS-TB_1x03-1MP_P1.25mm_Horizontal | ~
 |  | BL7 | Conn_01x03 | Connector_Generic:Conn_01x03 | Connector_JST:JST_GH_SM03B-GHS-TB_1x03-1MP_P1.25mm_Horizontal | ~
 |  | C1 | 1u | Device:C_Small | Capacitor_SMD:C_0603_1608Metric | ~
 |  | C2 | 10u | Device:C_Small | Capacitor_SMD:C_0603_1608Metric | ~
 |  | C3 | 10u | Device:C_Small | Capacitor_SMD:C_0603_1608Metric | ~
 |  | C4 | 1u | Device:C_Small | Capacitor_SMD:C_0402_1005Metric | ~
 |  | C5 | 1u | Device:C_Small | Capacitor_SMD:C_0402_1005Metric | ~
 |  | C6 | 0u1 | Device:C_Small | Capacitor_SMD:C_0402_1005Metric | ~
 |  | C7 | 0u1 | Device:C_Small | Capacitor_SMD:C_0402_1005Metric | ~
 |  | C8 | 10u | Device:C_Small | Capacitor_SMD:C_0603_1608Metric | ~
 |  | C9 | 10u | Device:C_Small | Capacitor_SMD:C_0603_1608Metric | ~
 |  | C10 | 1u | Device:C_Small | Capacitor_SMD:C_0402_1005Metric | ~
 |  | C11 | 1u | Device:C_Small | Capacitor_SMD:C_0402_1005Metric | ~
 |  | C12 | 0u1 | Device:C_Small | Capacitor_SMD:C_0402_1005Metric | ~
 |  | C13 | 0u1 | Device:C_Small | Capacitor_SMD:C_0402_1005Metric | ~
 |  | C14 | 0u1 | Device:C_Small | Capacitor_SMD:C_0402_1005Metric | ~
 |  | C15 | 0u1 | Device:C_Small | Capacitor_SMD:C_0402_1005Metric | ~
 |  | C16 | 0u1 | Device:C_Small | Capacitor_SMD:C_0402_1005Metric | ~
 |  | C17 | 0u1 | Device:C_Small | Capacitor_SMD:C_0402_1005Metric | ~
 |  | C18 | 1u | Device:C_Small | Capacitor_SMD:C_0402_1005Metric | ~
 |  | C19 | 1u | Device:C_Small | Capacitor_SMD:C_0402_1005Metric | ~
 |  | C20 | 1u | Device:C_Small | Capacitor_SMD:C_0402_1005Metric | ~
 |  | C21 | 1u | Device:C_Small | Capacitor_SMD:C_0402_1005Metric | ~
 |  | C22 | 0u1 | Device:C_Small | Capacitor_SMD:C_0402_1005Metric | ~
 |  | C23 | 0u1 | Device:C_Small | Capacitor_SMD:C_0402_1005Metric | ~
 |  | C24 | 0u1 | Device:C_Small | Capacitor_SMD:C_0402_1005Metric | ~
 |  | C25 | 0u1 | Device:C_Small | Capacitor_SMD:C_0402_1005Metric | ~
 |  | C26 | 1u | Device:C_Small | Capacitor_SMD:C_0402_1005Metric | ~
 |  | C27 | 1u | Device:C_Small | Capacitor_SMD:C_0402_1005Metric | ~
 |  | C28 | 1u | Device:C_Small | Capacitor_SMD:C_0402_1005Metric | ~
 |  | C29 | 1u | Device:C_Small | Capacitor_SMD:C_0402_1005Metric | ~
 |  | C30 | 100u | Device:C_Polarized_Small | Capacitor_Tantalum_SMD:CP_EIA-7343-31_Kemet-D | ~
 |  | C31 | 10u | Device:C_Small | Capacitor_SMD:C_0603_1608Metric | ~
 |  | C32 | 22u | Device:C_Small | Capacitor_SMD:C_0603_1608Metric | ~
 |  | C33 | 10u | Device:C_Small | Capacitor_SMD:C_0603_1608Metric | ~
 |  | C34 | 22u | Device:C_Small | Capacitor_SMD:C_0603_1608Metric | ~
 |  | C35 | 10nF | Device:C_Small | Capacitor_SMD:C_0402_1005Metric | ~
 |  | D1 | R_LED | Device:LED | LED_SMD:LED_0603_1608Metric_Pad1.05x0.95mm_HandSolder | ~
 |  | J1 | Conn_02x20_Odd_Even_Male | Connector_Generic:Conn_02x20_Odd_Even | Connector_PinHeader_1.27mm:PinHeader_2x20_P1.27mm_Vertical_SMD | ~
 |  | J2 | Conn_02x20_Odd_Even_Female | Connector_Generic:Conn_02x20_Odd_Even | Connector_PinHeader_1.27mm:PinHeader_2x20_P1.27mm_Vertical_SMD | ~
 |  | J3 | Conn_02x20_Odd_Even_Male | Connector_Generic:Conn_02x20_Odd_Even | Connector_PinHeader_1.27mm:PinHeader_2x20_P1.27mm_Vertical_SMD | ~
 |  | J4 | Conn_02x20_Odd_Even_Female | Connector_Generic:Conn_02x20_Odd_Even | Connector_PinHeader_1.27mm:PinHeader_2x20_P1.27mm_Vertical_SMD | ~
 |  | J5 | JST_PH_SM2 | Connector_Generic:Conn_01x02 | Connector_JST:JST_PH_S2B-PH-SM4-TB_1x02-1MP_P2.00mm_Horizontal | ~
 |  | JP1 | SolderJumper_2_Open | Jumper:SolderJumper_2_Open | Jumper:SolderJumper-2_P1.3mm_Open_RoundedPad1.0x1.5mm | ~
 |  | JP2 | SolderJumper_2_Open | Jumper:SolderJumper_2_Open | Jumper:SolderJumper-2_P1.3mm_Open_RoundedPad1.0x1.5mm | ~
 |  | JP3 | SolderJumper_2_Open | Jumper:SolderJumper_2_Open | Jumper:SolderJumper-2_P1.3mm_Open_RoundedPad1.0x1.5mm | ~
 |  | JP4 | SolderJumper_2_Open | Jumper:SolderJumper_2_Open | Jumper:SolderJumper-2_P1.3mm_Open_RoundedPad1.0x1.5mm | ~
 |  | JP5 | SolderJumper_2_Open | Jumper:SolderJumper_2_Open | Jumper:SolderJumper-2_P1.3mm_Open_RoundedPad1.0x1.5mm | ~
 |  | JP6 | SolderJumper_2_Open | Jumper:SolderJumper_2_Open | Jumper:SolderJumper-2_P1.3mm_Open_RoundedPad1.0x1.5mm | ~
 |  | JP7 | SolderJumper_2_Open | Jumper:SolderJumper_2_Open | Jumper:SolderJumper-2_P1.3mm_Open_RoundedPad1.0x1.5mm | ~
 |  | JP8 | SolderJumper_2_Open | Jumper:SolderJumper_2_Open | Jumper:SolderJumper-2_P1.3mm_Open_RoundedPad1.0x1.5mm | ~
 |  | JP9 | SolderJumper_2_Open | Jumper:SolderJumper_2_Open | Jumper:SolderJumper-2_P1.3mm_Open_RoundedPad1.0x1.5mm | ~
 |  | JP10 | SolderJumper_2_Open | Jumper:SolderJumper_2_Open | Jumper:SolderJumper-2_P1.3mm_Open_RoundedPad1.0x1.5mm | ~
 |  | JP11 | SolderJumper_2_Open | Jumper:SolderJumper_2_Open | Jumper:SolderJumper-2_P1.3mm_Open_RoundedPad1.0x1.5mm | ~
 |  | M0 | JST_SH_SM02 | Connector_Generic:Conn_01x02 | Connector_JST:JST_GH_SM02B-GHS-TB_1x02-1MP_P1.25mm_Horizontal | ~
 |  | M1 | JST_SH_SM02 | Connector_Generic:Conn_01x02 | Connector_JST:JST_GH_SM02B-GHS-TB_1x02-1MP_P1.25mm_Horizontal | ~
 |  | M2 | JST_SH_SM02 | Connector_Generic:Conn_01x02 | Connector_JST:JST_GH_SM02B-GHS-TB_1x02-1MP_P1.25mm_Horizontal | ~
 |  | M3 | JST_SH_SM02 | Connector_Generic:Conn_01x02 | Connector_JST:JST_GH_SM02B-GHS-TB_1x02-1MP_P1.25mm_Horizontal | ~
 |  | R1 | 10K | Device:R_Small | Resistor_SMD:R_0402_1005Metric | ~
 |  | R2 | 10K | Device:R_Small | Resistor_SMD:R_0402_1005Metric | ~
 |  | R3 | 10K | Device:R_Small | Resistor_SMD:R_0402_1005Metric | ~
 |  | R4 | 10K | Device:R_Small | Resistor_SMD:R_0402_1005Metric | ~
 |  | R5 | 10K | Device:R_Small | Resistor_SMD:R_0402_1005Metric | ~
 |  | R6 | 10K | Device:R_Small | Resistor_SMD:R_0402_1005Metric | ~
 |  | R7 | 10K | Device:R_Small | Resistor_SMD:R_0402_1005Metric | ~
 |  | R8 | 220R | Device:R_Small | Resistor_SMD:R_0402_1005Metric | ~
 |  | R9 | 55K | Device:R_Small | Resistor_SMD:R_0402_1005Metric | ~
 |  | R10 | 55K | Device:R_Small | Resistor_SMD:R_0402_1005Metric | ~
 |  | R11 | 62K | Device:R_Small | Resistor_SMD:R_0402_1005Metric | ~
 |  | R12 | 73K2 | Device:R_Small | Resistor_SMD:R_0402_1005Metric | ~
 |  | R13 | 75K | Device:R_Small | Resistor_SMD:R_0402_1005Metric | ~
 |  | R14 | 24K | Device:R_Small | Resistor_SMD:R_0402_1005Metric | ~
 |  | R15 | 100K | Device:R_Small | Resistor_SMD:R_0402_1005Metric | ~
 |  | R16 | 19K1 | Device:R_Small | Resistor_SMD:R_0402_1005Metric | ~
 |  | R17 | 10K | Device:R_Small | Resistor_SMD:R_0402_1005Metric | ~
 |  | R18 | 10K | Device:R_Small | Resistor_SMD:R_0402_1005Metric | ~
 |  | S0 | Conn_01x03 | Connector_Generic:Conn_01x03 | Connector_JST:JST_GH_SM03B-GHS-TB_1x03-1MP_P1.25mm_Horizontal | ~
 |  | S1 | Conn_01x03 | Connector_Generic:Conn_01x03 | Connector_JST:JST_GH_SM03B-GHS-TB_1x03-1MP_P1.25mm_Horizontal | ~
 |  | S2 | Conn_01x03 | Connector_Generic:Conn_01x03 | Connector_JST:JST_GH_SM03B-GHS-TB_1x03-1MP_P1.25mm_Horizontal | ~
 |  | S3 | Conn_01x03 | Connector_Generic:Conn_01x03 | Connector_JST:JST_GH_SM03B-GHS-TB_1x03-1MP_P1.25mm_Horizontal | ~
 |  | S4 | Conn_01x03 | Connector_Generic:Conn_01x03 | Connector_JST:JST_GH_SM03B-GHS-TB_1x03-1MP_P1.25mm_Horizontal | ~
 |  | S5 | Conn_01x03 | Connector_Generic:Conn_01x03 | Connector_JST:JST_GH_SM03B-GHS-TB_1x03-1MP_P1.25mm_Horizontal | ~
 |  | S6 | Conn_01x03 | Connector_Generic:Conn_01x03 | Connector_JST:JST_GH_SM03B-GHS-TB_1x03-1MP_P1.25mm_Horizontal | ~
 |  | S7 | Conn_01x03 | Connector_Generic:Conn_01x03 | Connector_JST:JST_GH_SM03B-GHS-TB_1x03-1MP_P1.25mm_Horizontal | ~
 |  | SW1 | SW_SPDT | Switch:SW_SPDT | Button_Switch_SMD:SW_SPDT_PCM12 | ~
 |  | SW2 | SW_SPDT | Switch:SW_SPDT | Button_Switch_SMD:SW_SPDT_PCM12 | ~
 |  | U1 | PCA9685BS | Driver_LED:PCA9685BS | Package_DFN_QFN:QFN-28-1EP_6x6mm_P0.65mm_EP4.25x4.25mm | http://www.nxp.com/documents/data_sheet/PCA9685.pdf
 |  | U2 | DRV8835DSSR | TI_Motor-Driver:DRV8835DSSR | Package_SON:WSON-12-1EP_3x2mm_P0.5mm_EP1x2.65_ThermalVias | https://www.ti.com/lit/ds/symlink/drv8835.pdf
 |  | U3 | DRV8835DSSR | TI_Motor-Driver:DRV8835DSSR | Package_SON:WSON-12-1EP_3x2mm_P0.5mm_EP1x2.65_ThermalVias | https://www.ti.com/lit/ds/symlink/drv8835.pdf
 |  | U4 | DRV8835DSSR | TI_Motor-Driver:DRV8835DSSR | Package_SON:WSON-12-1EP_3x2mm_P0.5mm_EP1x2.65_ThermalVias | https://www.ti.com/lit/ds/symlink/drv8835.pdf
 |  | U5 | DRV8835DSSR | TI_Motor-Driver:DRV8835DSSR | Package_SON:WSON-12-1EP_3x2mm_P0.5mm_EP1x2.65_ThermalVias | https://www.ti.com/lit/ds/symlink/drv8835.pdf
 |  | U6 | MPM3610 | Converter_DCDC_U:MPM3610 | Package_DFN_QFN_U:MPM3610_QFN-20_5x3mm | https://www.monolithicpower.com/en/documentview/productdocument/index/version/2/document_type/Datasheet/lang/en/sku/MPM3610GQV/document_id/2090/
 |  | U7 | MPM3610 | Converter_DCDC_U:MPM3610 | Package_DFN_QFN_U:MPM3610_QFN-20_5x3mm | https://www.monolithicpower.com/en/documentview/productdocument/index/version/2/document_type/Datasheet/lang/en/sku/MPM3610GQV/document_id/2090/
 |  | U8 | MAX17049G+T10 | M_Battery-Management:MAX17049G+T10 | M_Battery-Management:MAX17049GT10 | https://datasheets.maximintegrated.com/en/ds/MAX17048-MAX17049.pdf
 |  | U9 | TS5A3159ADCKR | Analog_Switch:TS5A3159ADCKR | Package_TO_SOT_SMD:SOT-363_SC-70-6 | http://www.ti.com/lit/ds/symlink/ts5a3159a.pdf
 |  | U10 | TS5A3159ADCKR | Analog_Switch:TS5A3159ADCKR | Package_TO_SOT_SMD:SOT-363_SC-70-6 | http://www.ti.com/lit/ds/symlink/ts5a3159a.pdf
Collated Components:
Item | Qty | Reference(s) | Value | LibPart | Footprint | Datasheet
1 | 16 | BL0, BL1, BL2, BL3, BL4, BL5, BL6, BL7, S0, S1, S2, S3, S4, S5, S6, S7 | Conn_01x03 | Connector_Generic:Conn_01x03 | Connector_JST:JST_GH_SM03B-GHS-TB_1x03-1MP_P1.25mm_Horizontal | ~
2 | 1 | C1 | 1u | Device:C_Small | Capacitor_SMD:C_0603_1608Metric | ~
3 | 6 | C2, C3, C8, C9, C31, C33 | 10u | Device:C_Small | Capacitor_SMD:C_0603_1608Metric | ~
4 | 12 | C4, C5, C10, C11, C18, C19, C20, C21, C26, C27, C28, C29 | 1u | Device:C_Small | Capacitor_SMD:C_0402_1005Metric | ~
5 | 12 | C6, C7, C12, C13, C14, C15, C16, C17, C22, C23, C24, C25 | 0u1 | Device:C_Small | Capacitor_SMD:C_0402_1005Metric | ~
6 | 1 | C30 | 100u | Device:C_Polarized_Small | Capacitor_Tantalum_SMD:CP_EIA-7343-31_Kemet-D | ~
7 | 2 | C32, C34 | 22u | Device:C_Small | Capacitor_SMD:C_0603_1608Metric | ~
8 | 1 | C35 | 10nF | Device:C_Small | Capacitor_SMD:C_0402_1005Metric | ~
9 | 1 | D1 | R_LED | Device:LED | LED_SMD:LED_0603_1608Metric_Pad1.05x0.95mm_HandSolder | ~
10 | 2 | J1, J3 | Conn_02x20_Odd_Even_Male | Connector_Generic:Conn_02x20_Odd_Even | Connector_PinHeader_1.27mm:PinHeader_2x20_P1.27mm_Vertical_SMD | ~
11 | 2 | J2, J4 | Conn_02x20_Odd_Even_Female | Connector_Generic:Conn_02x20_Odd_Even | Connector_PinHeader_1.27mm:PinHeader_2x20_P1.27mm_Vertical_SMD | ~
12 | 1 | J5 | JST_PH_SM2 | Connector_Generic:Conn_01x02 | Connector_JST:JST_PH_S2B-PH-SM4-TB_1x02-1MP_P2.00mm_Horizontal | ~
13 | 11 | JP1, JP2, JP3, JP4, JP5, JP6, JP7, JP8, JP9, JP10, JP11 | SolderJumper_2_Open | Jumper:SolderJumper_2_Open | Jumper:SolderJumper-2_P1.3mm_Open_RoundedPad1.0x1.5mm | ~
14 | 4 | M0, M1, M2, M3 | JST_SH_SM02 | Connector_Generic:Conn_01x02 | Connector_JST:JST_GH_SM02B-GHS-TB_1x02-1MP_P1.25mm_Horizontal | ~
15 | 9 | R1, R2, R3, R4, R5, R6, R7, R17, R18 | 10K | Device:R_Small | Resistor_SMD:R_0402_1005Metric | ~
16 | 1 | R8 | 220R | Device:R_Small | Resistor_SMD:R_0402_1005Metric | ~
17 | 2 | R9, R10 | 55K | Device:R_Small | Resistor_SMD:R_0402_1005Metric | ~
18 | 1 | R11 | 62K | Device:R_Small | Resistor_SMD:R_0402_1005Metric | ~
19 | 1 | R12 | 73K2 | Device:R_Small | Resistor_SMD:R_0402_1005Metric | ~
20 | 1 | R13 | 75K | Device:R_Small | Resistor_SMD:R_0402_1005Metric | ~
21 | 1 | R14 | 24K | Device:R_Small | Resistor_SMD:R_0402_1005Metric | ~
22 | 1 | R15 | 100K | Device:R_Small | Resistor_SMD:R_0402_1005Metric | ~
23 | 1 | R16 | 19K1 | Device:R_Small | Resistor_SMD:R_0402_1005Metric | ~
24 | 2 | SW1, SW2 | SW_SPDT | Switch:SW_SPDT | Button_Switch_SMD:SW_SPDT_PCM12 | ~
25 | 1 | U1 | PCA9685BS | Driver_LED:PCA9685BS | Package_DFN_QFN:QFN-28-1EP_6x6mm_P0.65mm_EP4.25x4.25mm | http://www.nxp.com/documents/data_sheet/PCA9685.pdf
26 | 4 | U2, U3, U4, U5 | DRV8835DSSR | TI_Motor-Driver:DRV8835DSSR | Package_SON:WSON-12-1EP_3x2mm_P0.5mm_EP1x2.65_ThermalVias | https://www.ti.com/lit/ds/symlink/drv8835.pdf
27 | 2 | U6, U7 | MPM3610 | Converter_DCDC_U:MPM3610 | Package_DFN_QFN_U:MPM3610_QFN-20_5x3mm | https://www.monolithicpower.com/en/documentview/productdocument/index/version/2/document_type/Datasheet/lang/en/sku/MPM3610GQV/document_id/2090/
28 | 1 | U8 | MAX17049G+T10 | M_Battery-Management:MAX17049G+T10 | M_Battery-Management:MAX17049GT10 | https://datasheets.maximintegrated.com/en/ds/MAX17048-MAX17049.pdf
29 | 2 | U9, U10 | TS5A3159ADCKR | Analog_Switch:TS5A3159ADCKR | Package_TO_SOT_SMD:SOT-363_SC-70-6 | http://www.ti.com/lit/ds/symlink/ts5a3159a.pdf

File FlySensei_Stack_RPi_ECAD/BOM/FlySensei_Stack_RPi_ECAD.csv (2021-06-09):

Source: | /Users/joseph/Onedrive_JPM/OneDrive - George Mason University/Classwork/Research/Project_BlimpSquad/PCB/FlySensei_Stack_ECAD/FlySensei_Stack_RPi_ECAD/FlySensei_Stack_RPi_ECAD.kicad_sch
Date: | Monday, June 07, 2021 at 06:19:09 PM
Tool: | Eeschema (5.99.0-10720-gd84fcd89f1)
Generator: | /Applications/KiCad/KiCad.app/Contents/SharedSupport/plugins/bom_csv_grouped_by_value.py
Component Count: | 93
Individual Components:
Item | Qty | Reference(s) | Value | LibPart | Footprint | Datasheet | Field4 | Field5 | Field6 | Field7 | Field8 | MANUFACTURER | MAXIMUM_PACKAGE_HEIGHT | PARTREV | Part Description | STANDARD
 |  | C1 | 0u1 16V | Device:C_Small | Capacitor_SMD:C_0402_1005Metric | ~
 |  | C2 | 0u1 16V | Device:C_Small | Capacitor_SMD:C_0402_1005Metric | ~
 |  | C3 | 0u1 16V | Device:C_Small | Capacitor_SMD:C_0402_1005Metric | ~
 |  | C4 | 0u1 16V | Device:C_Small | Capacitor_SMD:C_0402_1005Metric | ~
 |  | C5 | 0u1 6.3V | Device:C_Small | Capacitor_SMD:C_0402_1005Metric | ~
 |  | C6 | 0u1 6.3V | Device:C_Small | Capacitor_SMD:C_0402_1005Metric | ~
 |  | C7 | 0u1 6.3V | Device:C_Small | Capacitor_SMD:C_0402_1005Metric | ~
 |  | C8 | 0u1 6.3V | Device:C_Small | Capacitor_SMD:C_0402_1005Metric | ~
 |  | C9 | 0u1 6.3V | Device:C_Small | Capacitor_SMD:C_0402_1005Metric | ~
 |  | C10 | 0u1 6.3V | Device:C_Small | Capacitor_SMD:C_0402_1005Metric | ~
 |  | C11 | 22u 16V | Device:C_Small | Capacitor_SMD:C_0603_1608Metric | ~
 |  | C12 | 1u 16V | Device:C_Small | Capacitor_SMD:C_0603_1608Metric | ~
 |  | C13 | 10u 35v | Device:C | Capacitor_SMD:C_0805_2012Metric | https://www.murata.com/en-global/products/productdetail.aspx?partno=GRM21BC8YA106ME11%23 | Digikey | 490-10505-1-ND | GRM21BC8YA106KE11L | Murata |  |  |  |  | 10uF 10% or 20% 35V Ceramic Capacitor X6S 0805 (2012 Metric)
 |  | C14 | 10u 35v | Device:C | Capacitor_SMD:C_0805_2012Metric | https://www.murata.com/en-global/products/productdetail.aspx?partno=GRM21BC8YA106ME11%23 | Digikey | 490-10505-1-ND | GRM21BC8YA106KE11L | Murata |  |  |  |  | 10uF 10% or 20% 35V Ceramic Capacitor X6S 0805 (2012 Metric)
 |  | C15 | 100n 35V | Device:C | Capacitor_SMD:C_0402_1005Metric | https://search.murata.co.jp/Ceramy/image/img/A01X/G101/ENG/GRM155R71C104KA88-01.pdf | Farnell | 2611911 | RM EMK105 B7104KV-F | TAIYO YUDEN EUROPE GMBH | 110091611 |  |  |  | 0.1uF 10% 16V Ceramic Capacitor X7R 0402 (1005 Metric)
 |  | C16 | 10u 35V | Device:C_Small | Capacitor_SMD:C_0603_1608Metric | ~
 |  | C17 | 100n 35V | Device:C | Capacitor_SMD:C_0402_1005Metric | https://search.murata.co.jp/Ceramy/image/img/A01X/G101/ENG/GRM155R71C104KA88-01.pdf | Farnell | 2611911 | RM EMK105 B7104KV-F | TAIYO YUDEN EUROPE GMBH | 110091611 |  |  |  | 0.1uF 10% 16V Ceramic Capacitor X7R 0402 (1005 Metric)
 |  | C18 | 100uF | Device:CP | Capacitor_Tantalum_SMD:CP_EIA-7343-31_Kemet-D | ~ | Mouser | 667-EEF-CX0J101R |  |  |  |  |  |  | Capacitor, SP-Cap, 100u, 6.3V, 15mR ESR
 |  | C19 | 22u 16V | Device:C_Small | Capacitor_SMD:C_0603_1608Metric | ~
 |  | C20 | 1nf 16V | Device:C | Capacitor_SMD:C_0402_1005Metric | ~
 |  | C21 | 1.2nF 16V | Device:C | Capacitor_SMD:C_0402_1005Metric | http://www.farnell.com/datasheets/2734135.pdf | Digikey | 490-16429-1-ND | GCM155R71H122KA37D | Murata |  |  |  |  | 1200pF 10% 10V Ceramic Capacitor X5R 0402 (1005 Metric)
 |  | C22 | 1nf 16V | Device:C | Capacitor_SMD:C_0402_1005Metric | http://www.farnell.com/datasheets/2048267.pdf | Farnell | 2666374 | GRM1555C1H221JA01D | Murata |  |  |  |  | 220 pF, 50 V, 0402 [1005 Metric], ± 5%, C0G / NP0/CH, GCM Series
 |  | C23 | 22u 16V | Device:C | Capacitor_SMD:C_0805_2012Metric | https://search.murata.co.jp/Ceramy/image/img/A01X/G101/ENG/GRM21BR71A106KA73-01.pdf | Digikey | 490-14381-1-ND | GRM21BR71A106KA73L | Murata | 111893011 |  |  |  | 10uF 10% 10V Ceramic Capacitor X7R 0805 (2012 Metric)
 |  | C24 | 22u 16V | Device:C | Capacitor_SMD:C_0805_2012Metric | https://search.murata.co.jp/Ceramy/image/img/A01X/G101/ENG/GRM21BR71A106KA73-01.pdf | Digikey | 490-14381-1-ND | GRM21BR71A106KA73L | Murata | 111893011 |  |  |  | 10uF 10% 10V Ceramic Capacitor X7R 0805 (2012 Metric)
 |  | C25 | 22u 16V | Device:C | Capacitor_SMD:C_0805_2012Metric | https://search.murata.co.jp/Ceramy/image/img/A01X/G101/ENG/GRM21BR71A106KA73-01.pdf | Digikey | 490-14381-1-ND | GRM21BR71A106KA73L | Murata | 111893011 |  |  |  | 10uF 10% 10V Ceramic Capacitor X7R 0805 (2012 Metric)
 |  | C26 | 22u | Device:C_Small | Capacitor_SMD:C_0805_2012Metric | ~
 |  | C27 | 10u | Device:C | Capacitor_SMD:C_0805_2012Metric | https://search.murata.co.jp/Ceramy/image/img/A01X/G101/ENG/GRM21BR71A106KA73-01.pdf | Digikey | 490-14381-1-ND | GRM21BR71A106KA73L | Murata | 111893011 |  |  |  | 10uF 10% 10V Ceramic Capacitor X7R 0805 (2012 Metric)
 |  | D1 | LED_GRN | Device:LED_Small | LED_SMD:LED_0603_1608Metric | ~
 |  | D2 | LED_GRN | Device:LED_Small | LED_SMD:LED_0603_1608Metric | ~
 |  | D3 | LED_AMB | Device:LED_Small | LED_SMD:LED_0603_1608Metric | ~
 |  | D4 | LED_RED | Device:LED_Small | LED_SMD:LED_0603_1608Metric | ~
 |  | D5 | D_Schottky | Device:D_Schottky | Diode_SMD:D_SMB | ~
 |  | D6 | D_Schottky | Device:D_Schottky | Diode_SMD:D_SMB | ~
 |  | D7 | D_Schottky | Device:D_Schottky | Diode_SMD:D_SMB | ~
 |  | D8 | LED_WHT | Device:LED | LED_SMD:LED_0603_1608Metric | ~
 |  | H1 | MountingHole | Mechanical:MountingHole | MountingHole:MountingHole_2.7mm_M2.5_Pad_Via | ~
 |  | H2 | MountingHole | Mechanical:MountingHole | MountingHole:MountingHole_2.7mm_M2.5_Pad_Via | ~
 |  | H3 | MountingHole | Mechanical:MountingHole | MountingHole:MountingHole_2.7mm_M2.5_Pad_Via | ~
 |  | H4 | MountingHole | Mechanical:MountingHole | MountingHole:MountingHole_2.7mm_M2.5_Pad_Via | ~
 |  | J1 | Conn_01x03 | Connector_Generic:Conn_01x03 | Connector_PinHeader_1.00mm:PinHeader_1x03_P1.00mm_Vertical | ~
 |  | J2 | USB_C_Receptacle_USB2.0 | Connector:USB_C_Receptacle_USB2.0 | Connector_USB:USB_C_Receptacle_XKB_U262-16XN-4BVC11 | https://www.usb.org/sites/default/files/documents/usb_type-c.zip
 |  | J3 | Conn_02x20_Odd_Even_Male | Connector_Generic:Conn_02x20_Odd_Even | Connector_PinHeader_1.27mm:PinHeader_2x20_P1.27mm_Vertical_SMD | ~
 |  | J4 | Conn_02x20_Odd_Even_Female | Connector_Generic:Conn_02x20_Odd_Even | Connector_PinHeader_1.27mm:PinHeader_2x20_P1.27mm_Vertical_SMD | ~
 |  | J5 | Conn_02x20_Odd_Even_Male | Connector_Generic:Conn_02x20_Odd_Even | Connector_PinHeader_1.27mm:PinHeader_2x20_P1.27mm_Vertical_SMD | ~
 |  | J6 | Conn_02x20_Odd_Even_Female | Connector_Generic:Conn_02x20_Odd_Even | Connector_PinHeader_1.27mm:PinHeader_2x20_P1.27mm_Vertical_SMD | ~
 |  | J7 | Conn_01x22_Female | Connector:Conn_01x22_Female | Connector_FFC-FPC:Hirose_FH12-22S-0.5SH_1x22-1MP_P0.50mm_Horizontal | ~ | Mouser | 798-FH12-22S-0.5SH55 | FH12-22S-0.5SH55 | Hirose |  |  |  |  | 22 Position FFC, FPC Connector Contacts, Bottom 0.020" (0.50mm) Surface Mount, Right Angle
 |  | J8 | Conn_01x22_Female | Connector:Conn_01x22_Female | Connector_FFC-FPC:Hirose_FH12-22S-0.5SH_1x22-1MP_P0.50mm_Horizontal | ~ | Mouser | 798-FH12-22S-0.5SH55 | FH12-22S-0.5SH55 | Hirose |  |  |  |  | 22 Position FFC, FPC Connector Contacts, Bottom 0.020" (0.50mm) Surface Mount, Right Angle
 |  | J9 | Conn_01x14_Female | Connector:Conn_01x14_Female | Connector_FFC-FPC:Hirose_FH12-14S-0.5SH_1x14-1MP_P0.50mm_Horizontal | ~
 |  | J10 | Micro_SD_Card_Det | Connector:Micro_SD_Card_Det | RPi_CM4IO:SDCARD_MOLEX_503398-1892 | https://www.hirose.com/product/en/download_file/key_name/DM3/category/Catalog/doc_file_id/49662/?item_id=195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 | Farnell | 2358234 | 503398-1892 | Molex | UCON00512 |  |  |  | 9 (8 + 1) Position Card Connector microSD™ Surface Mount, Right Angle Gold
 |  | JP1 | SolderJumper_2_Open | Jumper:SolderJumper_2_Open | Jumper:SolderJumper-2_P1.3mm_Open_RoundedPad1.0x1.5mm | ~
 |  | JP2 | SolderJumper_2_Open | Jumper:SolderJumper_2_Open | Jumper:SolderJumper-2_P1.3mm_Open_RoundedPad1.0x1.5mm | ~
 |  | JP3 | SolderJumper_2_Open | Jumper:SolderJumper_2_Open | Jumper:SolderJumper-2_P1.3mm_Open_RoundedPad1.0x1.5mm | ~
 |  | JP4 | SolderJumper_2_Open | Jumper:SolderJumper_2_Open | Jumper:SolderJumper-2_P1.3mm_Open_RoundedPad1.0x1.5mm | ~
 |  | JP5 | SolderJumper_2_Open | Jumper:SolderJumper_2_Open | Jumper:SolderJumper-2_P1.3mm_Open_RoundedPad1.0x1.5mm | ~
 |  | JP6 | SolderJumper_2_Open | Jumper:SolderJumper_2_Open | Jumper:SolderJumper-2_P1.3mm_Open_RoundedPad1.0x1.5mm | ~
 |  | JP7 | SolderJumper_3_Open | Jumper:SolderJumper_3_Open | Jumper:SolderJumper-3_P1.3mm_Open_RoundedPad1.0x1.5mm | ~
 |  | L1 | SRN6045TA-3R3Y | pspice:INDUCTOR | Inductor_SMD:L_Bourns_SRN6045TA | https://www.bourns.com/docs/Product-Datasheets/SRN6045TA.pdf | Farnell | 2616889 | SRN6045TA-3R3Y | Bourns |  |  |  |  | 3.3µH Semi-Shielded Wirewound Inductor 7.8A 21mOhm Nonstandard
 |  | Q1 | Q_NMOS_GSD | Device:Q_NMOS_GSD | Package_TO_SOT_SMD:SOT-23 | ~
 |  | R1 | 270R | Device:R_Small | Resistor_SMD:R_0402_1005Metric | ~
 |  | R2 | 270R | Device:R_Small | Resistor_SMD:R_0402_1005Metric | ~
 |  | R3 | 270R | Device:R_Small | Resistor_SMD:R_0402_1005Metric | ~
 |  | R4 | 270R | Device:R_Small | Resistor_SMD:R_0402_1005Metric | ~
 |  | R5 | 4.7K | Device:R_Small | Resistor_SMD:R_0402_1005Metric | ~
 |  | R6 | 900K | Device:R_Small | Resistor_SMD:R_0402_1005Metric | ~
 |  | R7 | 50K | Device:R_Small | Resistor_SMD:R_0402_1005Metric | ~
 |  | R8 | 10R | Device:R | Resistor_SMD:R_0402_1005Metric | https://fscdn.rohm.com/en/products/databook/datasheet/passive/resistor/chip_resistor/mcr-e.pdf | Farnell | 9238999 | RC0402FR-0710RL | Yageo | URES00256 |  |  |  | Resistor 10R M1005 1% 63mW
 |  | R9 | 55K | Device:R_Small | Resistor_SMD:R_0402_1005Metric | ~
 |  | R10 | 62K | Device:R_Small | Resistor_SMD:R_0402_1005Metric | ~
 |  | R11 | 20K 1% | Device:R | Resistor_SMD:R_0402_1005Metric | https://fscdn.rohm.com/en/products/databook/datasheet/passive/resistor/chip_resistor/mcr-e.pdf | Farnell | 2331485 | RK73H1ETTP2002F | KOA EUROPE GMBH |  |  |  |  | Resistor 20K M1005 1% 63mW
 |  | R12 | 12K 1% | Device:R | Resistor_SMD:R_0402_1005Metric | https://fscdn.rohm.com/en/products/databook/datasheet/passive/resistor/chip_resistor/mcr-e.pdf | Farnell | 9239367 | MCR01MZPF1202 | Rohm |  |  |  |  | Resistor 12K M1005 1% 63mW
 |  | R13 | 2.2K 1% | Device:R | Resistor_SMD:R_0402_1005Metric | https://fscdn.rohm.com/en/products/databook/datasheet/passive/resistor/chip_resistor/mcr-e.pdf | Farnell | 9239278 | RK73G1ETQTP2201D | KOA EUROPE GMBH | 120889581 |  |  |  | Resistor 2.2K M1005 1% 63mW
 |  | R14 | 75K | Device:R_Small | Resistor_SMD:R_0402_1005Metric | ~
 |  | R15 | 24K | Device:R_Small | Resistor_SMD:R_0402_1005Metric | ~
 |  | R16 | 10K | Device:R_Small | Resistor_SMD:R_0402_1005Metric | ~
 |  | R17 | 10K | Device:R_Small | Resistor_SMD:R_0402_1005Metric | ~
 |  | R18 | 10K | Device:R_Small | Resistor_SMD:R_0402_1005Metric | ~
 |  | R19 | 10K | Device:R_Small | Resistor_SMD:R_0402_1005Metric | ~
 |  | R20 | 12K | Device:R | Resistor_SMD:R_0402_1005Metric | https://fscdn.rohm.com/en/products/databook/datasheet/passive/resistor/chip_resistor/mcr-e.pdf | Farnell | 9239367 | MCR01MZPF1202 | Rohm |  |  |  |  | Resistor 12K M1005 1% 63mW
 |  | R21 | 480 | Device:R_Small | Resistor_SMD:R_0402_1005Metric | ~
 |  | SW1 | SW_SPST | Switch:SW_SPST | Button_Switch_SMD:Panasonic_EVQPUL_EVQPUC | ~
 |  | SW2 | SW_SPDT | Switch:SW_SPDT | Button_Switch_SMD:SW_SPDT_PCM12 | ~
 |  | SW3 | SW_SPDT | Switch:SW_SPDT | Button_Switch_SMD:SW_SPDT_PCM12 | ~
 |  | U1 | ComputeModule4-CM4 | RPi_CM4IO:ComputeModule4-CM4 | RPi_CM4IO:Raspberry-Pi-4-Compute-Module | https://datasheets.raspberrypi.org/cm4/cm4-datasheet.pdf | Hirose | 2x DF40C-100DS-0.4V
 |  | U2 | ATtiny85V-10S | MCU_Microchip_ATtiny:ATtiny85V-10S | Package_SO:SOIC-8W_5.3x5.3mm_P1.27mm | http://ww1.microchip.com/downloads/en/DeviceDoc/atmel-2586-avr-8-bit-microcontroller-attiny25-attiny45-attiny85_datasheet.pdf
 |  | U3 | 74LVC1G07 | RPi_CM4IO:74LVC1G07 | Package_TO_SOT_SMD:SOT-353_SC-70-5 | http://www.ti.com/lit/sg/scyt129e/scyt129e.pdf
 |  | U4 | G313-06329-00 | AI_Coral:G313-06329-00 | AI_Coral:G313-06329-00 | https://coral.ai/static/files/Coral-Accelerator-Module-datasheet.pdf |  |  |  |  |  | Coral | 1.55 mm | 1.3 |  | Manufacturer Recommendations
 |  | U5 | TPD2EUSB30 | Power_Protection:TPD2EUSB30 | Package_TO_SOT_SMD:Texas_DRT-3 | http://www.ti.com/lit/ds/symlink/tpd2eusb30a.pdf
 |  | U6 | TUSB321 | Interface_USB:TUSB321 | Package_DFN_QFN:Texas_X2QFN-12_1.6x1.6mm_P0.4mm | http://www.ti.com/lit/ds/symlink/tusb321.pdf
 |  | U7 | MPM3610 | Converter_DCDC_U:MPM3610 | Package_DFN_QFN_U:MPM3610_QFN-20_5x3mm | https://www.monolithicpower.com/en/documentview/productdocument/index/version/2/document_type/Datasheet/lang/en/sku/MPM3610GQV/document_id/2090/
 |  | U8 | TPD4EUSB30 | Power_Protection:TPD4EUSB30 | Package_SON:USON-10_2.5x1.0mm_P0.5mm | http://www.ti.com/lit/ds/symlink/tpd2eusb30a.pdf
 |  | U9 | TPD4EUSB30 | Power_Protection:TPD4EUSB30 | Package_SON:USON-10_2.5x1.0mm_P0.5mm | http://www.ti.com/lit/ds/symlink/tpd2eusb30a.pdf
 |  | U10 | RT9742GGJ5 | CM4IO:RT9742GGJ5 | Package_TO_SOT_SMD:SOT-23-5 | https://www.richtek.com/assets/product_file/RT9742/DS9742-00.pdf | Farnell | 2545875 | RT9742GGJ5 | RichTek | USWI00166 |  |  |  | Power Switch/Driver 1:1 N-Channel 1A TSOT-23-5
 |  | U16 | AP64501SP-13 | RPi_CM4IO:AP64351 | Package_SO:SOIC-8-1EP_3.9x4.9mm_P1.27mm_EP2.95x4.9mm_Mask2.71x3.4mm_ThermalVias | https://www.diodes.com/assets/Datasheets/AP64501.pdf | Digikey | 31-AP64501SP-13CT-ND | AP64501SP-13 | Diodes |  |  |  |  | Buck Switching Regulator IC Positive Adjustable 0.8V 1 Output 5A 8-SOIC (0.154", 3.90mm Width) Exposed Pad
Collated Components:
Item | Qty | Reference(s) | Value | LibPart | Footprint | Datasheet | Field4 | Field5 | Field6 | Field7 | Field8 | MANUFACTURER | MAXIMUM_PACKAGE_HEIGHT | PARTREV | Part Description | STANDARD
1 | 4 | C1, C2, C3, C4 | 0u1 16V | Device:C_Small | Capacitor_SMD:C_0402_1005Metric | ~
2 | 6 | C5, C6, C7, C8, C9, C10 | 0u1 6.3V | Device:C_Small | Capacitor_SMD:C_0402_1005Metric | ~
3 | 2 | C11, C19 | 22u 16V | Device:C_Small | Capacitor_SMD:C_0603_1608Metric | ~
4 | 1 | C12 | 1u 16V | Device:C_Small | Capacitor_SMD:C_0603_1608Metric | ~
5 | 2 | C13, C14 | 10u 35v | Device:C | Capacitor_SMD:C_0805_2012Metric | https://www.murata.com/en-global/products/productdetail.aspx?partno=GRM21BC8YA106ME11%23 | Digikey | 490-10505-1-ND | GRM21BC8YA106KE11L | Murata |  |  |  |  | 10uF 10% or 20% 35V Ceramic Capacitor X6S 0805 (2012 Metric)
6 | 2 | C15, C17 | 100n 35V | Device:C | Capacitor_SMD:C_0402_1005Metric | https://search.murata.co.jp/Ceramy/image/img/A01X/G101/ENG/GRM155R71C104KA88-01.pdf | Farnell | 2611911 | RM EMK105 B7104KV-F | TAIYO YUDEN EUROPE GMBH | 110091611 |  |  |  | 0.1uF 10% 16V Ceramic Capacitor X7R 0402 (1005 Metric)
7 | 1 | C16 | 10u 35V | Device:C_Small | Capacitor_SMD:C_0603_1608Metric | ~
8 | 1 | C18 | 100uF | Device:CP | Capacitor_Tantalum_SMD:CP_EIA-7343-31_Kemet-D | ~ | Mouser | 667-EEF-CX0J101R |  |  |  |  |  |  | Capacitor, SP-Cap, 100u, 6.3V, 15mR ESR
9 | 2 | C20, C22 | 1nf 16V | Device:C | Capacitor_SMD:C_0402_1005Metric | ~ | Farnell | 2666374 | GRM1555C1H221JA01D | Murata |  |  |  |  | 220 pF, 50 V, 0402 [1005 Metric], ± 5%, C0G / NP0/CH, GCM Series
10 | 1 | C21 | 1.2nF 16V | Device:C | Capacitor_SMD:C_0402_1005Metric | http://www.farnell.com/datasheets/2734135.pdf | Digikey | 490-16429-1-ND | GCM155R71H122KA37D | Murata |  |  |  |  | 1200pF 10% 10V Ceramic Capacitor X5R 0402 (1005 Metric)
11 | 3 | C23, C24, C25 | 22u 16V | Device:C | Capacitor_SMD:C_0805_2012Metric | https://search.murata.co.jp/Ceramy/image/img/A01X/G101/ENG/GRM21BR71A106KA73-01.pdf | Digikey | 490-14381-1-ND | GRM21BR71A106KA73L | Murata | 111893011 |  |  |  | 10uF 10% 10V Ceramic Capacitor X7R 0805 (2012 Metric)
12 | 1 | C26 | 22u | Device:C_Small | Capacitor_SMD:C_0805_2012Metric | ~
13 | 1 | C27 | 10u | Device:C | Capacitor_SMD:C_0805_2012Metric | https://search.murata.co.jp/Ceramy/image/img/A01X/G101/ENG/GRM21BR71A106KA73-01.pdf | Digikey | 490-14381-1-ND | GRM21BR71A106KA73L | Murata | 111893011 |  |  |  | 10uF 10% 10V Ceramic Capacitor X7R 0805 (2012 Metric)
14 | 2 | D1, D2 | LED_GRN | Device:LED_Small | LED_SMD:LED_0603_1608Metric | ~
15 | 1 | D3 | LED_AMB | Device:LED_Small | LED_SMD:LED_0603_1608Metric | ~
16 | 1 | D4 | LED_RED | Device:LED_Small | LED_SMD:LED_0603_1608Metric | ~
17 | 3 | D5, D6, D7 | D_Schottky | Device:D_Schottky | Diode_SMD:D_SMB | ~
18 | 1 | D8 | LED_WHT | Device:LED | LED_SMD:LED_0603_1608Metric | ~
19 | 4 | H1, H2, H3, H4 | MountingHole | Mechanical:MountingHole | MountingHole:MountingHole_2.7mm_M2.5_Pad_Via | ~
20 | 1 | J1 | Conn_01x03 | Connector_Generic:Conn_01x03 | Connector_PinHeader_1.00mm:PinHeader_1x03_P1.00mm_Vertical | ~
21 | 1 | J2 | USB_C_Receptacle_USB2.0 | Connector:USB_C_Receptacle_USB2.0 | Connector_USB:USB_C_Receptacle_XKB_U262-16XN-4BVC11 | https://www.usb.org/sites/default/files/documents/usb_type-c.zip
22 | 2 | J3, J5 | Conn_02x20_Odd_Even_Male | Connector_Generic:Conn_02x20_Odd_Even | Connector_PinHeader_1.27mm:PinHeader_2x20_P1.27mm_Vertical_SMD | ~
23 | 2 | J4, J6 | Conn_02x20_Odd_Even_Female | Connector_Generic:Conn_02x20_Odd_Even | Connector_PinHeader_1.27mm:PinHeader_2x20_P1.27mm_Vertical_SMD | ~
24 | 2 | J7, J8 | Conn_01x22_Female | Connector:Conn_01x22_Female | Connector_FFC-FPC:Hirose_FH12-22S-0.5SH_1x22-1MP_P0.50mm_Horizontal | ~ | Mouser | 798-FH12-22S-0.5SH55 | FH12-22S-0.5SH55 | Hirose |  |  |  |  | 22 Position FFC, FPC Connector Contacts, Bottom 0.020" (0.50mm) Surface Mount, Right Angle
25 | 1 | J9 | Conn_01x14_Female | Connector:Conn_01x14_Female | Connector_FFC-FPC:Hirose_FH12-14S-0.5SH_1x14-1MP_P0.50mm_Horizontal | ~
26 | 1 | J10 | Micro_SD_Card_Det | Connector:Micro_SD_Card_Det | RPi_CM4IO:SDCARD_MOLEX_503398-1892 | https://www.hirose.com/product/en/download_file/key_name/DM3/category/Catalog/doc_file_id/49662/?item_id=195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 | Farnell | 2358234 | 503398-1892 | Molex | UCON00512 |  |  |  | 9 (8 + 1) Position Card Connector microSD™ Surface Mount, Right Angle Gold
27 | 6 | JP1, JP2, JP3, JP4, JP5, JP6 | SolderJumper_2_Open | Jumper:SolderJumper_2_Open | Jumper:SolderJumper-2_P1.3mm_Open_RoundedPad1.0x1.5mm | ~
28 | 1 | JP7 | SolderJumper_3_Open | Jumper:SolderJumper_3_Open | Jumper:SolderJumper-3_P1.3mm_Open_RoundedPad1.0x1.5mm | ~
29 | 1 | L1 | SRN6045TA-3R3Y | pspice:INDUCTOR | Inductor_SMD:L_Bourns_SRN6045TA | https://www.bourns.com/docs/Product-Datasheets/SRN6045TA.pdf | Farnell | 2616889 | SRN6045TA-3R3Y | Bourns |  |  |  |  | 3.3µH Semi-Shielded Wirewound Inductor 7.8A 21mOhm Nonstandard
30 | 1 | Q1 | Q_NMOS_GSD | Device:Q_NMOS_GSD | Package_TO_SOT_SMD:SOT-23 | ~
31 | 4 | R1, R2, R3, R4 | 270R | Device:R_Small | Resistor_SMD:R_0402_1005Metric | ~
32 | 1 | R5 | 4.7K | Device:R_Small | Resistor_SMD:R_0402_1005Metric | ~
33 | 1 | R6 | 900K | Device:R_Small | Resistor_SMD:R_0402_1005Metric | ~
34 | 1 | R7 | 50K | Device:R_Small | Resistor_SMD:R_0402_1005Metric | ~
35 | 1 | R8 | 10R | Device:R | Resistor_SMD:R_0402_1005Metric | https://fscdn.rohm.com/en/products/databook/datasheet/passive/resistor/chip_resistor/mcr-e.pdf | Farnell | 9238999 | RC0402FR-0710RL | Yageo | URES00256 |  |  |  | Resistor 10R M1005 1% 63mW
36 | 1 | R9 | 55K | Device:R_Small | Resistor_SMD:R_0402_1005Metric | ~
37 | 1 | R10 | 62K | Device:R_Small | Resistor_SMD:R_0402_1005Metric | ~
38 | 1 | R11 | 20K 1% | Device:R | Resistor_SMD:R_0402_1005Metric | https://fscdn.rohm.com/en/products/databook/datasheet/passive/resistor/chip_resistor/mcr-e.pdf | Farnell | 2331485 | RK73H1ETTP2002F | KOA EUROPE GMBH |  |  |  |  | Resistor 20K M1005 1% 63mW
39 | 1 | R12 | 12K 1% | Device:R | Resistor_SMD:R_0402_1005Metric | https://fscdn.rohm.com/en/products/databook/datasheet/passive/resistor/chip_resistor/mcr-e.pdf | Farnell | 9239367 | MCR01MZPF1202 | Rohm |  |  |  |  | Resistor 12K M1005 1% 63mW
40 | 1 | R13 | 2.2K 1% | Device:R | Resistor_SMD:R_0402_1005Metric | https://fscdn.rohm.com/en/products/databook/datasheet/passive/resistor/chip_resistor/mcr-e.pdf | Farnell | 9239278 | RK73G1ETQTP2201D | KOA EUROPE GMBH | 120889581 |  |  |  | Resistor 2.2K M1005 1% 63mW
41 | 1 | R14 | 75K | Device:R_Small | Resistor_SMD:R_0402_1005Metric | ~
42 | 1 | R15 | 24K | Device:R_Small | Resistor_SMD:R_0402_1005Metric | ~
43 | 4 | R16, R17, R18, R19 | 10K | Device:R_Small | Resistor_SMD:R_0402_1005Metric | ~
44 | 1 | R20 | 12K | Device:R | Resistor_SMD:R_0402_1005Metric | https://fscdn.rohm.com/en/products/databook/datasheet/passive/resistor/chip_resistor/mcr-e.pdf | Farnell | 9239367 | MCR01MZPF1202 | Rohm |  |  |  |  | Resistor 12K M1005 1% 63mW
45 | 1 | R21 | 480R | Device:R_Small | Resistor_SMD:R_0402_1005Metric | ~
46 | 1 | SW1 | SW_SPST | Switch:SW_SPST | Button_Switch_SMD:Panasonic_EVQPUL_EVQPUC | ~
47 | 2 | SW2, SW3 | SW_SPDT | Switch:SW_SPDT | Button_Switch_SMD:SW_SPDT_PCM12 | ~
48 | 1 | U1 | ComputeModule4-CM4 | RPi_CM4IO:ComputeModule4-CM4 | RPi_CM4IO:Raspberry-Pi-4-Compute-Module | https://datasheets.raspberrypi.org/cm4/cm4-datasheet.pdf | Hirose | 2x DF40C-100DS-0.4V
49 | 1 | U2 | ATtiny85V-10S | MCU_Microchip_ATtiny:ATtiny85V-10S | Package_SO:SOIC-8W_5.3x5.3mm_P1.27mm | http://ww1.microchip.com/downloads/en/DeviceDoc/atmel-2586-avr-8-bit-microcontroller-attiny25-attiny45-attiny85_datasheet.pdf
50 | 1 | U3 | 74LVC1G07 | RPi_CM4IO:74LVC1G07 | Package_TO_SOT_SMD:SOT-353_SC-70-5 | http://www.ti.com/lit/sg/scyt129e/scyt129e.pdf
51 | 1 | U4 | G313-06329-00 | AI_Coral:G313-06329-00 | AI_Coral:G313-06329-00 | https://coral.ai/static/files/Coral-Accelerator-Module-datasheet.pdf |  |  |  |  |  | Coral | 1.55 mm | 1.3 |  | Manufacturer Recommendations
52 | 1 | U5 | TPD2EUSB30 | Power_Protection:TPD2EUSB30 | Package_TO_SOT_SMD:Texas_DRT-3 | http://www.ti.com/lit/ds/symlink/tpd2eusb30a.pdf
53 | 1 | U6 | TUSB321 | Interface_USB:TUSB321 | Package_DFN_QFN:Texas_X2QFN-12_1.6x1.6mm_P0.4mm | http://www.ti.com/lit/ds/symlink/tusb321.pdf
54 | 1 | U7 | MPM3610 | Converter_DCDC_U:MPM3610 | Package_DFN_QFN_U:MPM3610_QFN-20_5x3mm | https://www.monolithicpower.com/en/documentview/productdocument/index/version/2/document_type/Datasheet/lang/en/sku/MPM3610GQV/document_id/2090/
55 | 2 | U8, U9 | TPD4EUSB30 | Power_Protection:TPD4EUSB30 | Package_SON:USON-10_2.5x1.0mm_P0.5mm | http://www.ti.com/lit/ds/symlink/tpd2eusb30a.pdf
56 | 1 | U10 | RT9742GGJ5 | CM4IO:RT9742GGJ5 | Package_TO_SOT_SMD:SOT-23-5 | https://www.richtek.com/assets/product_file/RT9742/DS9742-00.pdf | Farnell | 2545875 | RT9742GGJ5 | RichTek | USWI00166 |  |  |  | Power Switch/Driver 1:1 N-Channel 1A TSOT-23-5
57 | 1 | U16 | AP64501SP-13 | RPi_CM4IO:AP64351 | Package_SO:SOIC-8-1EP_3.9x4.9mm_P1.27mm_EP2.95x4.9mm_Mask2.71x3.4mm_ThermalVias | https://www.diodes.com/assets/Datasheets/AP64501.pdf | Digikey | 31-AP64501SP-13CT-ND | AP64501SP-13 | Diodes |  |  |  |  | Buck Switching Regulator IC Positive Adjustable 0.8V 1 Output 5A 8-SOIC (0.154", 3.90mm Width) Exposed Pad

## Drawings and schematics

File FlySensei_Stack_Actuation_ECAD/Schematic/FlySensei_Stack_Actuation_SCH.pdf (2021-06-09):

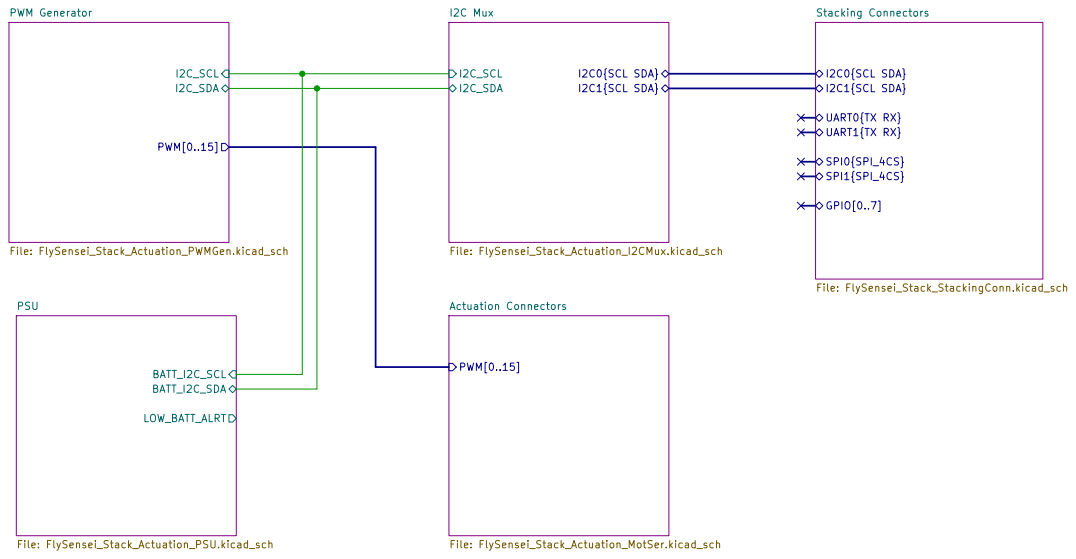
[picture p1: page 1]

I2C0{SCL SDA} Actuation Connectors File: FlySensei_Stack_Actuation_MotSer.kicad_sch
I2C_SDA

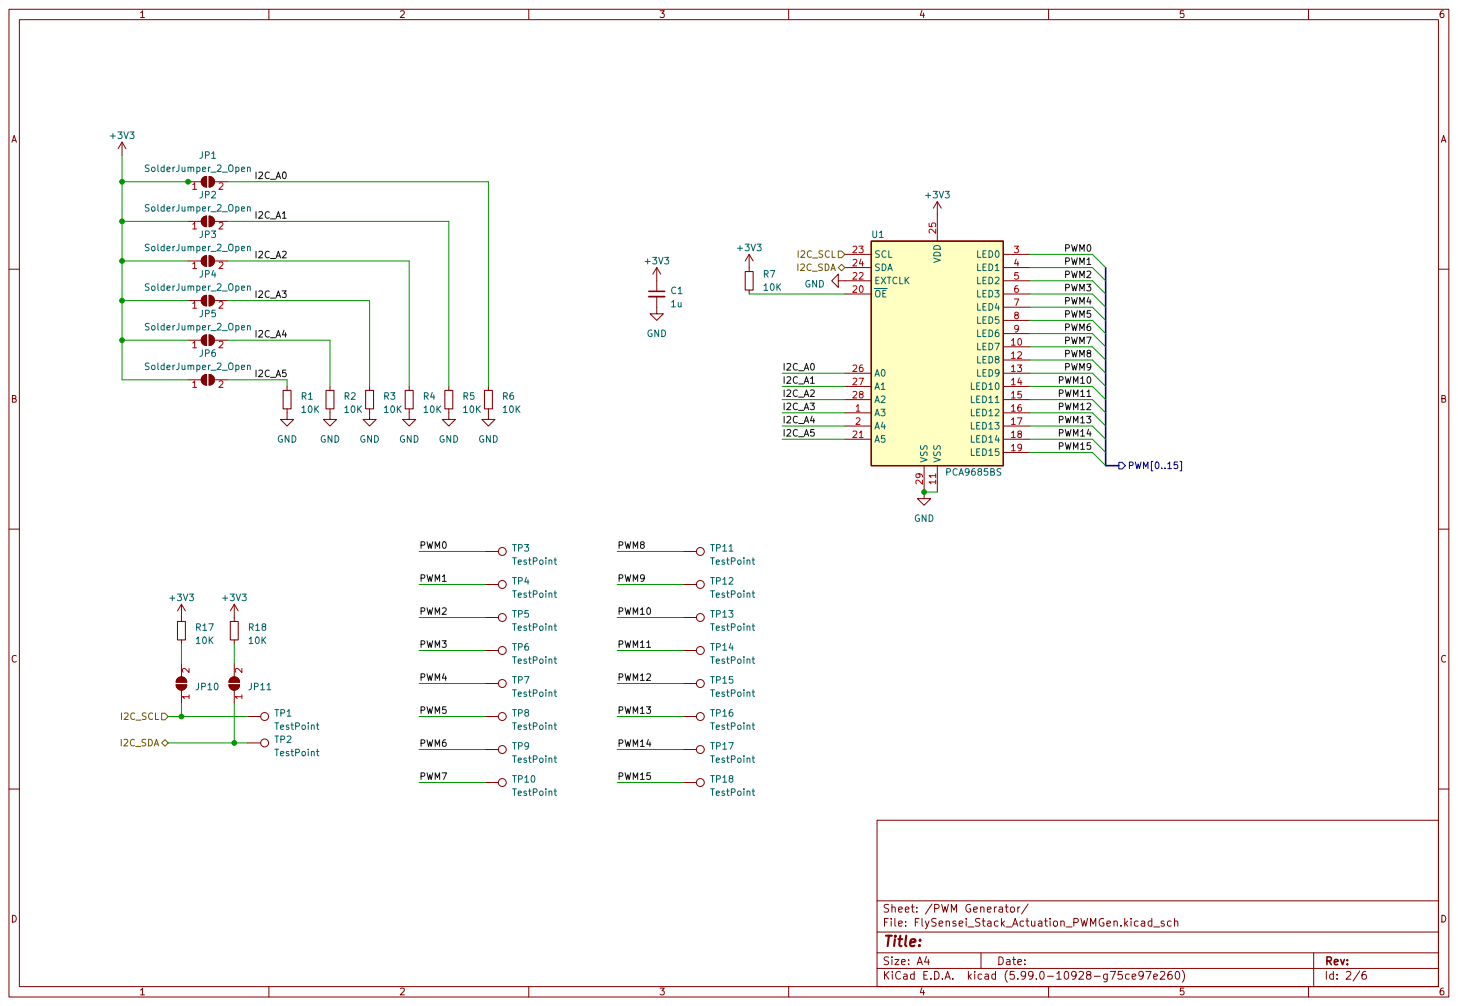
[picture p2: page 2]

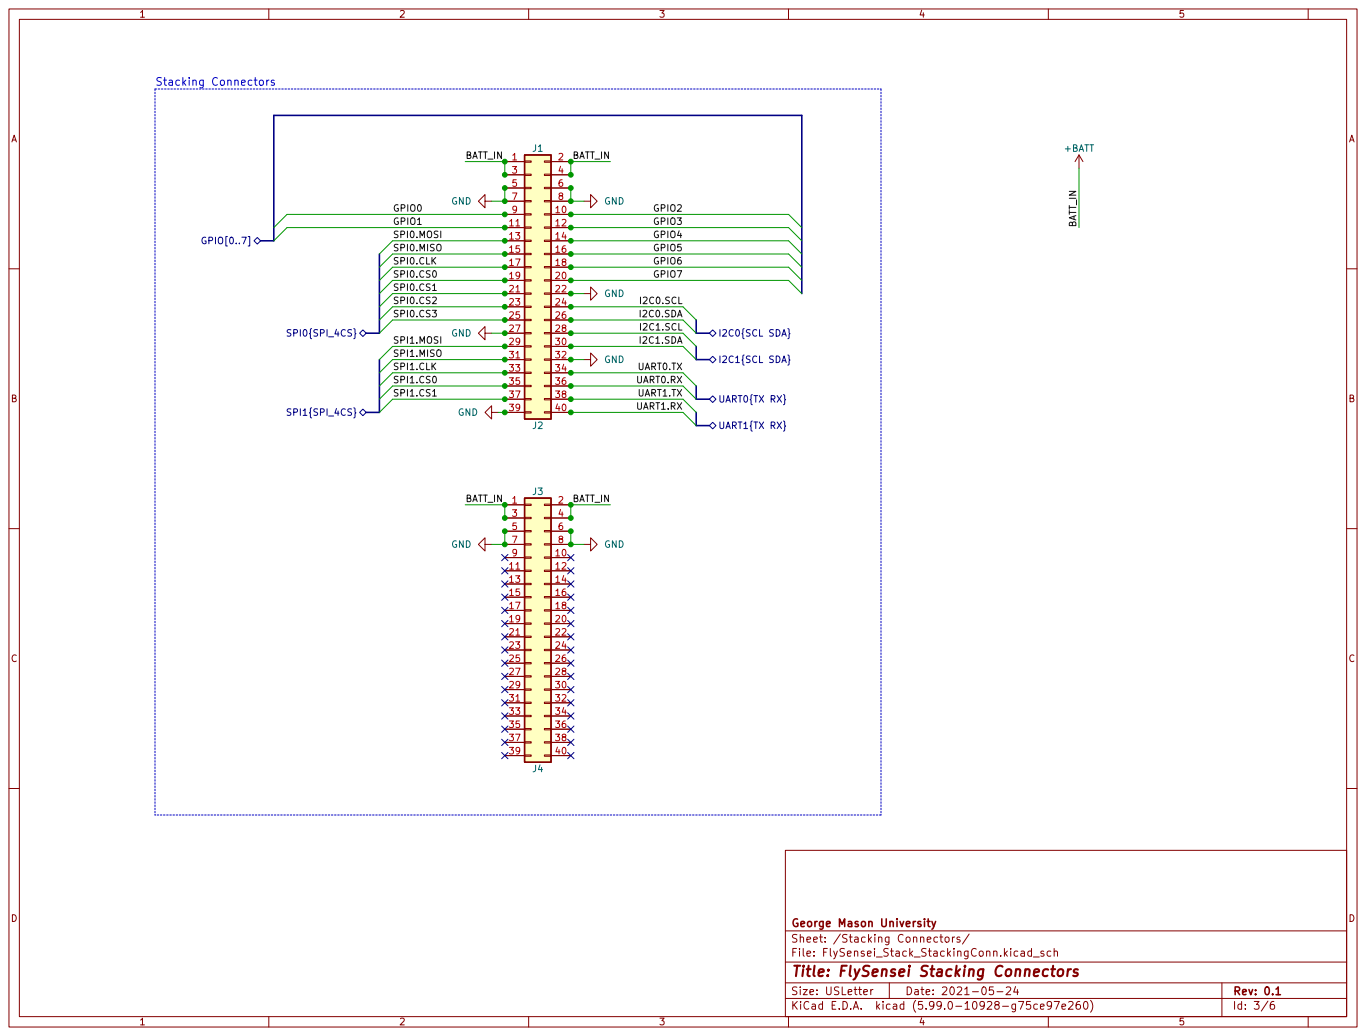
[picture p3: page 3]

George Mason University
Sheet: /Stacking Connectors/
File: FlySensei_Stack_StackingConn.kicad_sch
Id: 3/6 Title: FlySensei Stacking Connectors

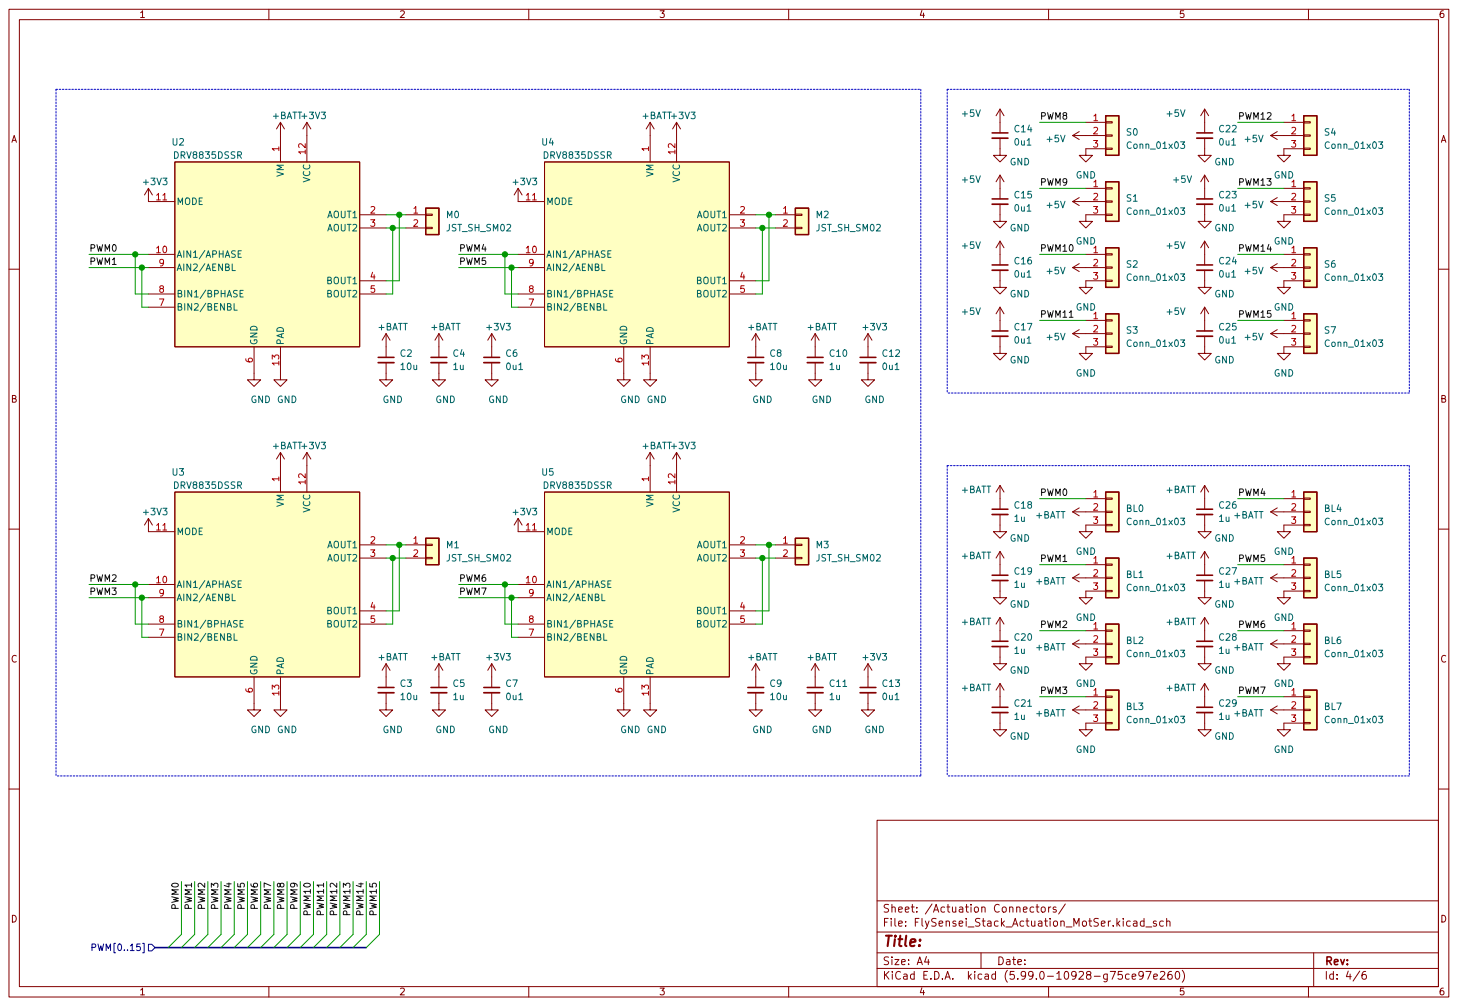
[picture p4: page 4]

1 AIN1/APHASE 10 MODE 11 VCC 12 PAD 13 AOUT1 2 AOUT2 3 BOUT1 4 BOUT2 5 GND

6 BIN2/BENBL 7 BIN1/BPHASE 8 AIN2/AENBL 9 U5DRV8835DSSR GND

File: FlySensei_Stack_Actuation_MotSer.kicad_sch Sheet: /Actuation Connectors/
Id: 4/6 Title:

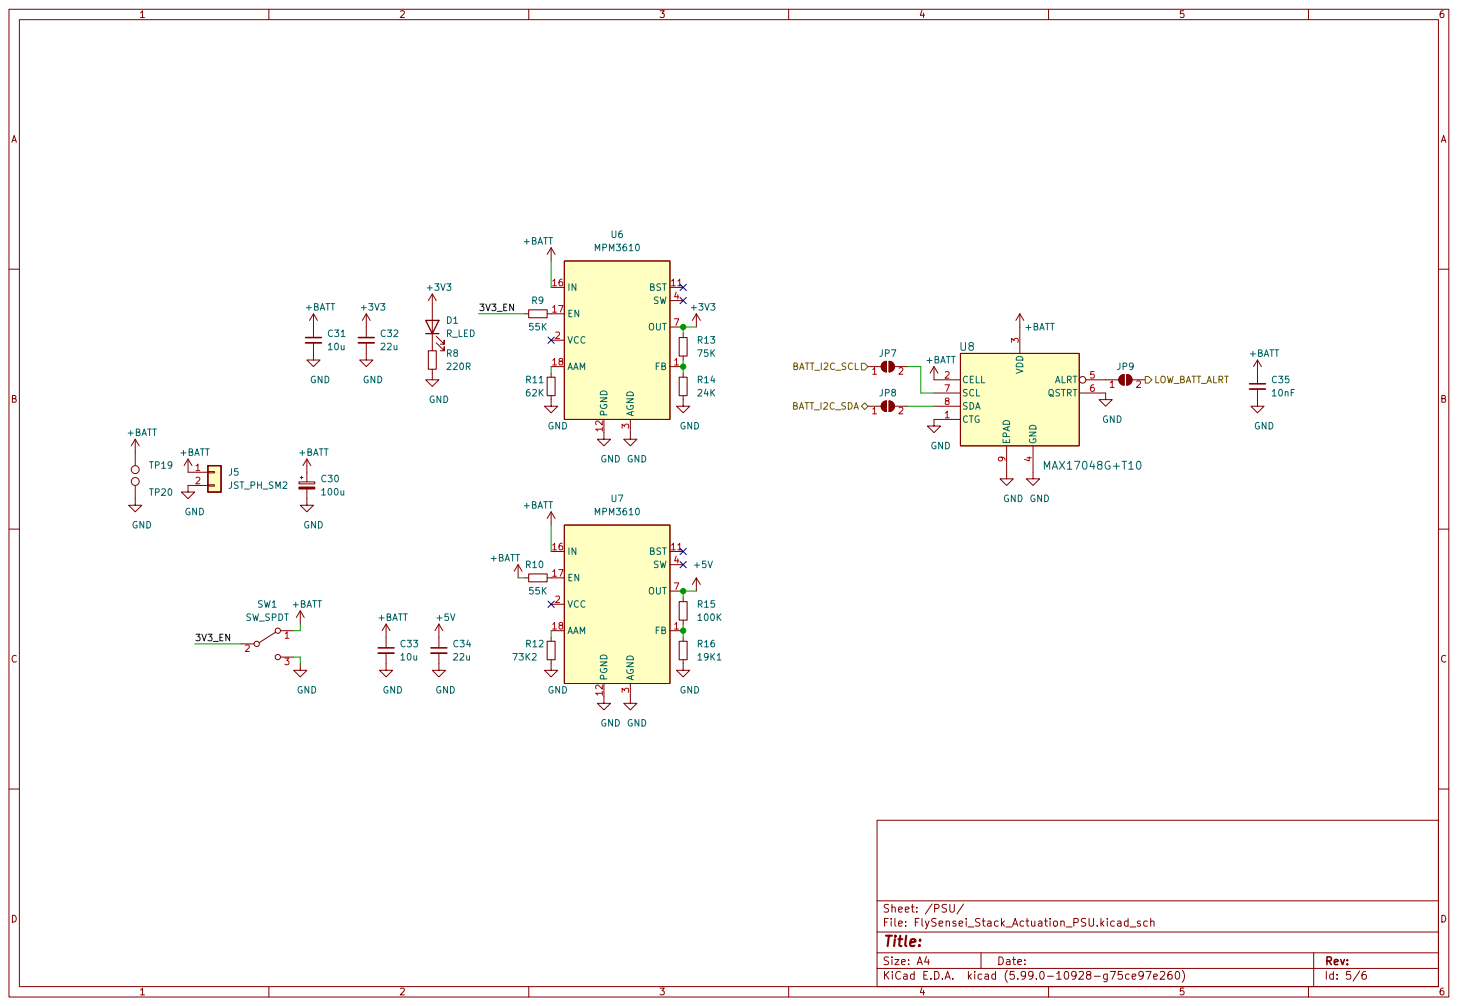
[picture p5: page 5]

3 SW 4 OUT 7 U6 MPM3610 FB 1 BST 11 PGND 12

4 ALRT 5 QSTRT 6 SCL 7 SDA 8 EPAD

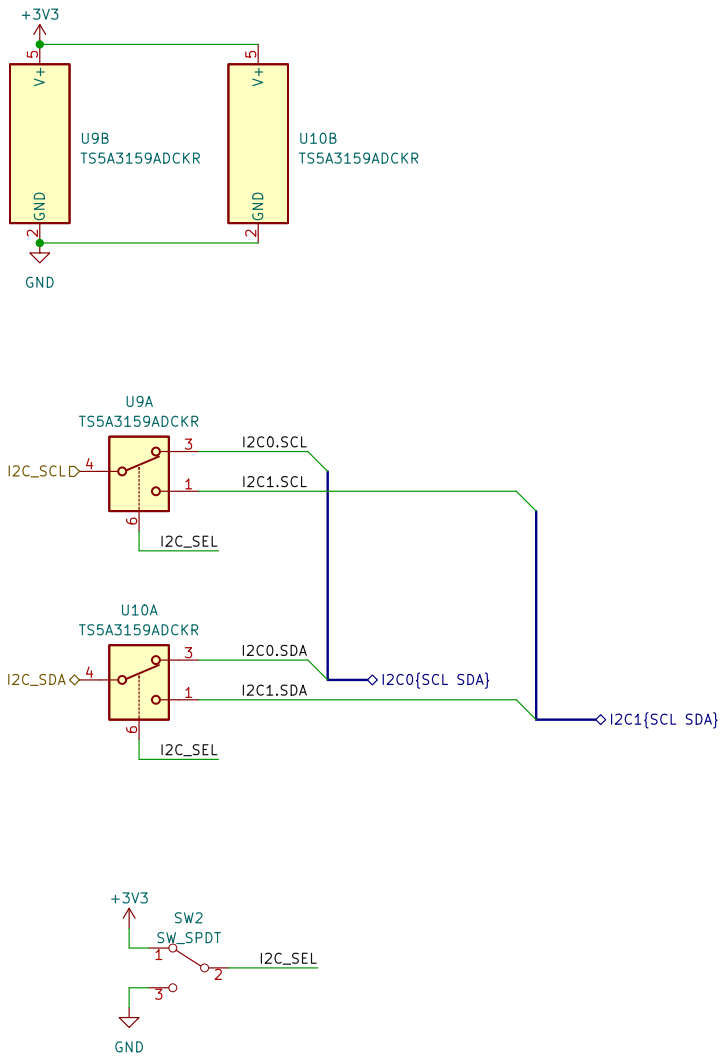
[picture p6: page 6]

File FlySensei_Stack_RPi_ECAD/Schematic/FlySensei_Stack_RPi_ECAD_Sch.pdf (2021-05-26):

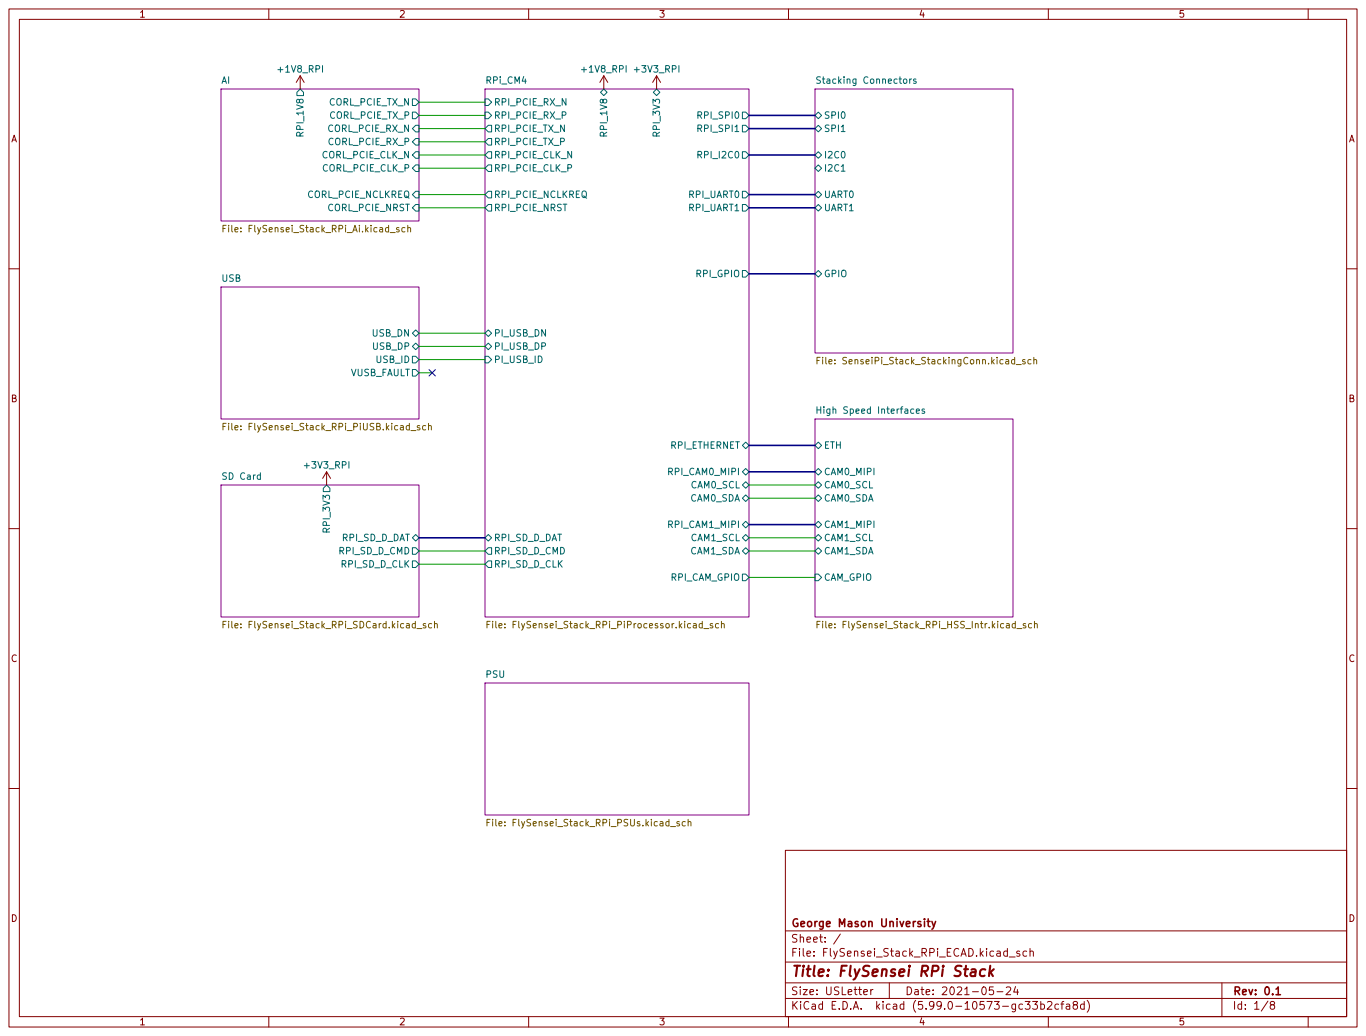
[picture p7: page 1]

File: FlySensei_Stack_RPi_PSUs.kicad_sch SD Card File: FlySensei_Stack_RPi_SDCard.kicad_sch RPI_SD_D_DAT RPI_SD_D_CLK RPI_SD_D_CMD RPI_3V3 USB

File: FlySensei_Stack_RPi_ECAD.kicad_sch Sheet: / George Mason University

Id: 1/8 Title: FlySensei RPi Stack

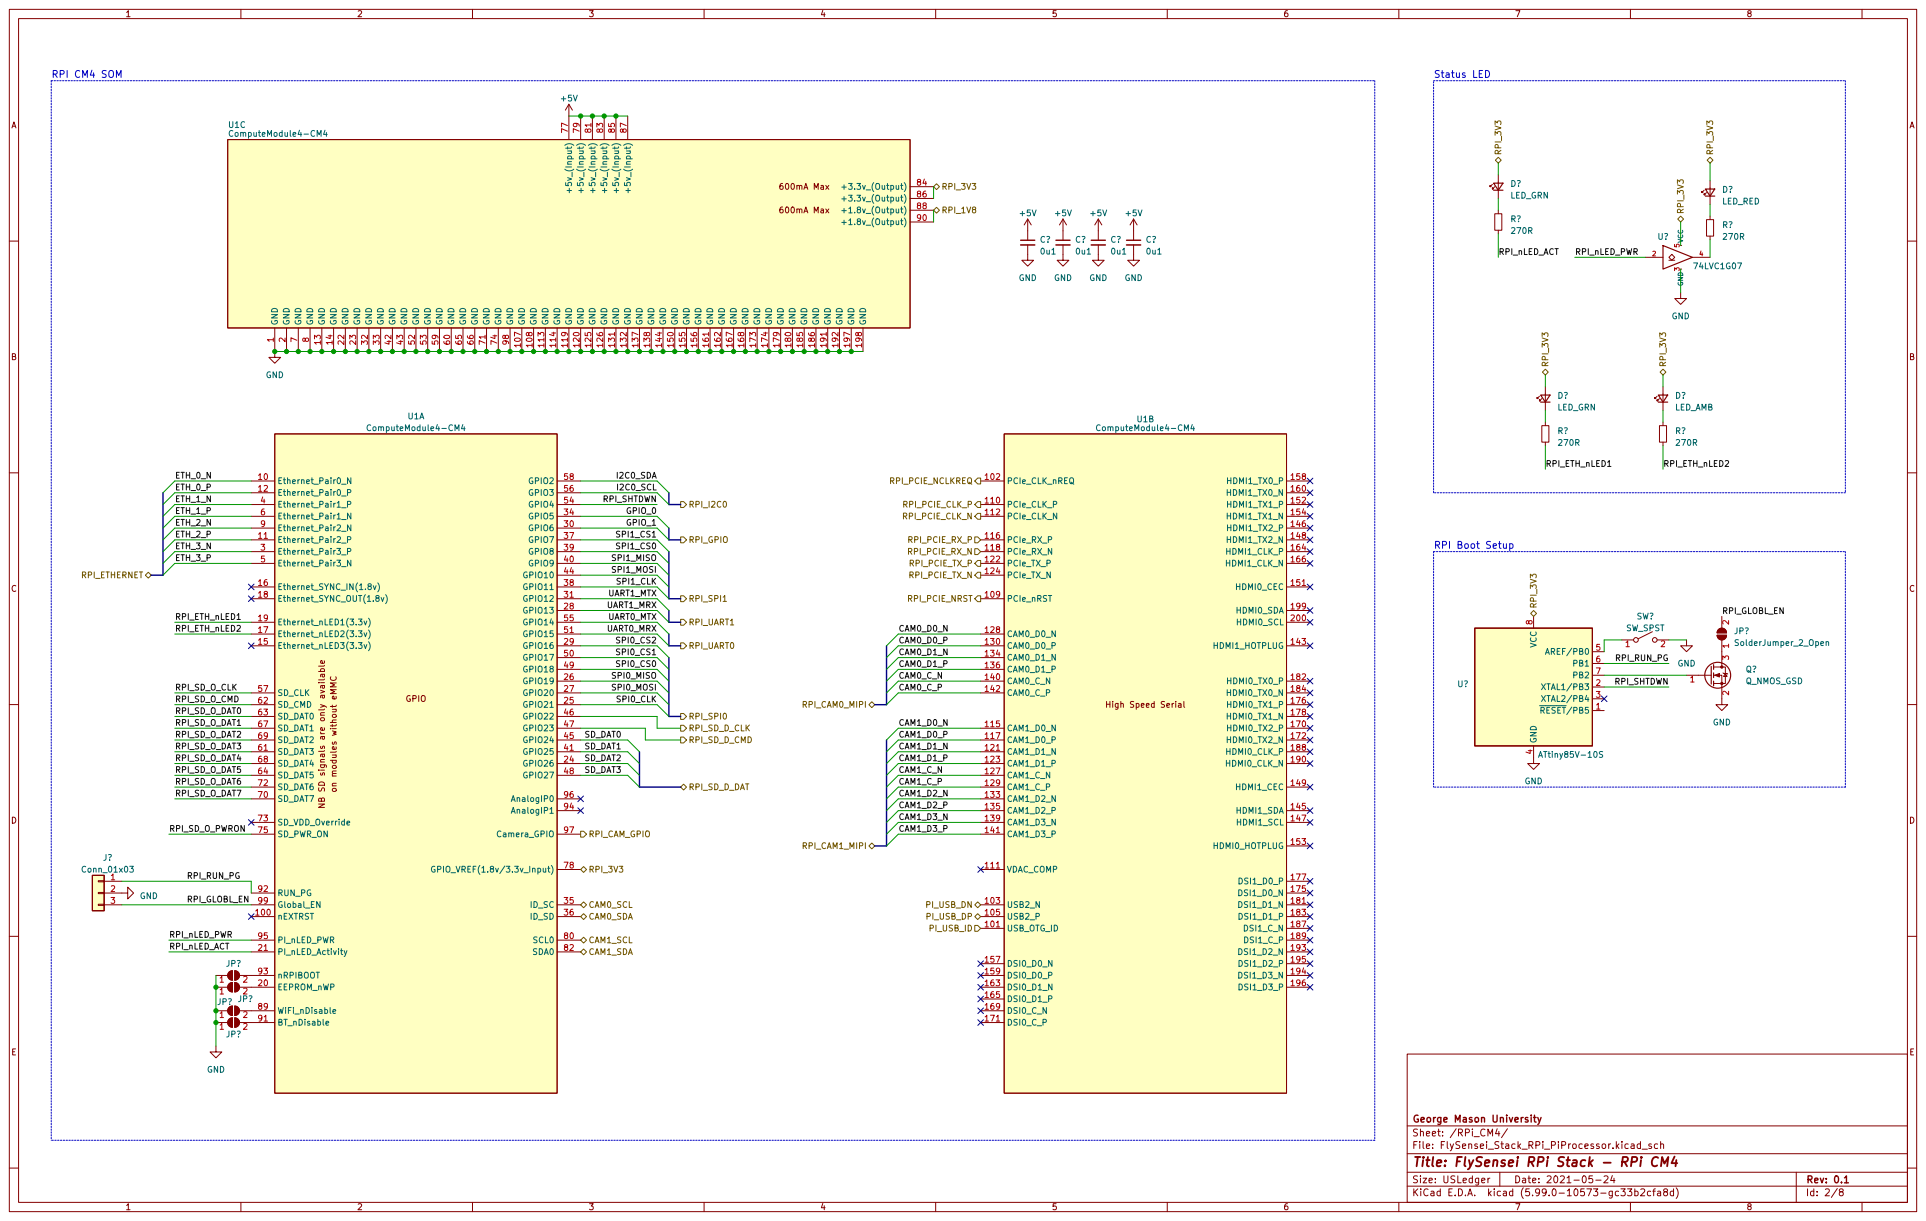
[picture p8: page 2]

7 GND 71 GND 74 +5v_(Input) 77 +5v_(Input) 79 GND

1 GND 107 GND 108 GND 113 GND 114 GND 119 GND 120 GND 125 GND 126 GND 13 GND 131 GND 132 GND 137 GND 138 GND 14 GND 144 GND 150 GND 155 GND 156 GND 161 GND 162 GND 167 GND 168 GND 173 GND 174 GND 179 GND 180 GND 185 GND 186 GND 191 GND 192 GND 197 GND 198 GND
SD_DAT2 SD_DAT0SPI0_CLK UART1_MRX

2 GND 22 GND 23 GND 32 GND 33 GND 42 GND 43 GND 52 GND 53 GND 59 GND 60 GND 65 GND 66 GND

JP? SolderJumper_2_Open GPIO NB SD signals are only available on modules without eMMC

George Mason University
Sheet: /RPi_CM4/
File: FlySensei_Stack_RPi_PiProcessor.kicad_sch
Id: 2/8 Title: FlySensei RPi Stack - RPi CM4

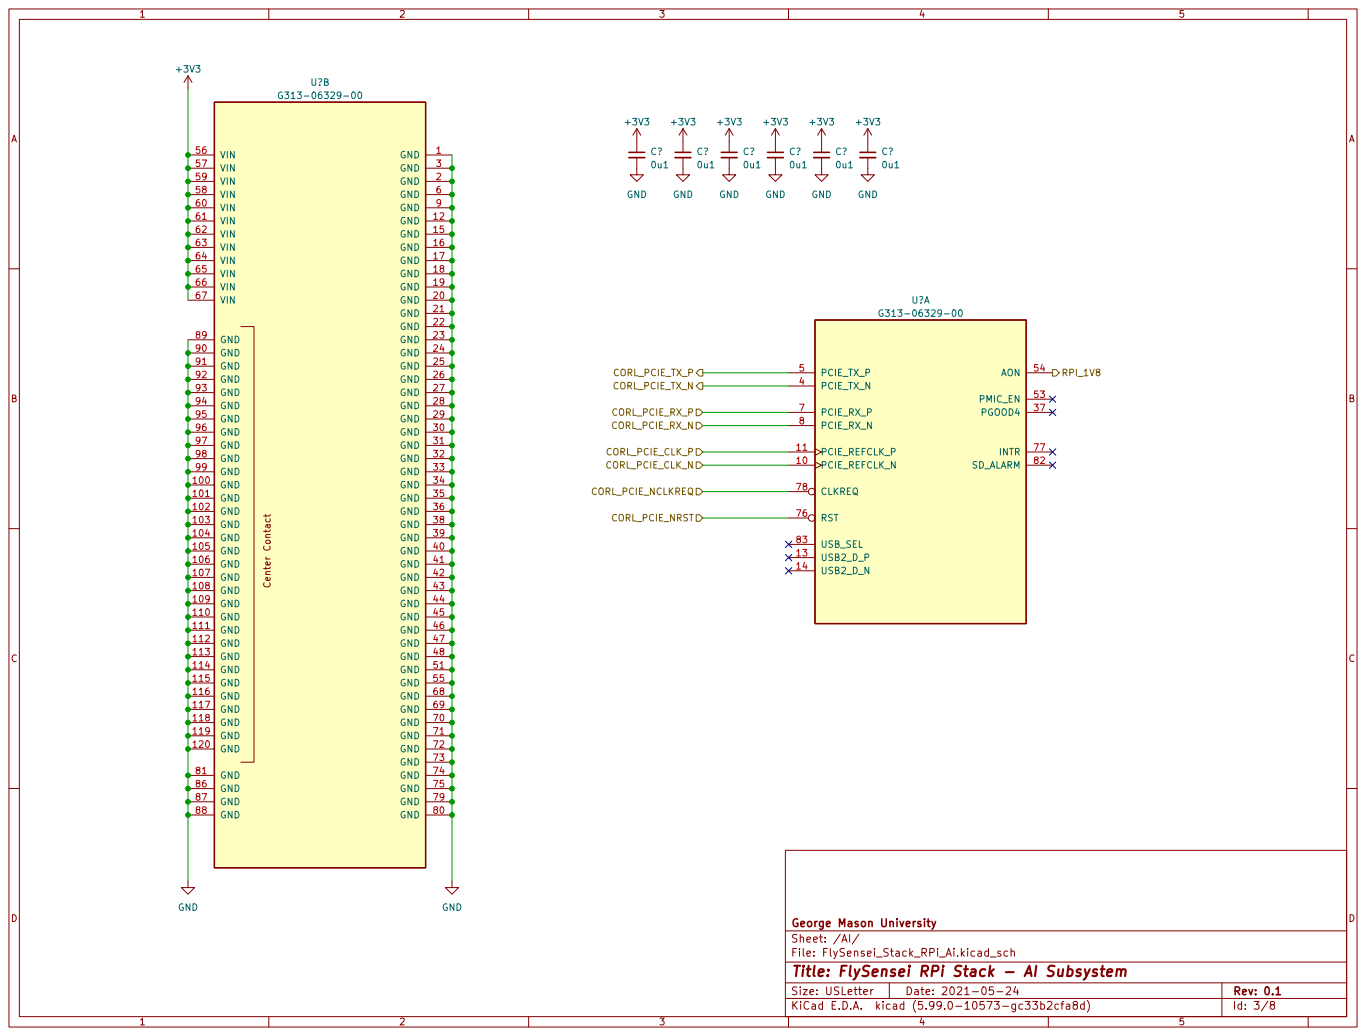
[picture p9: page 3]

File: FlySensei_Stack_RPi_Ai.kicad_sch Sheet: /AI/ George Mason University

Id: 3/8 Title: FlySensei RPi Stack - AI Subsystem

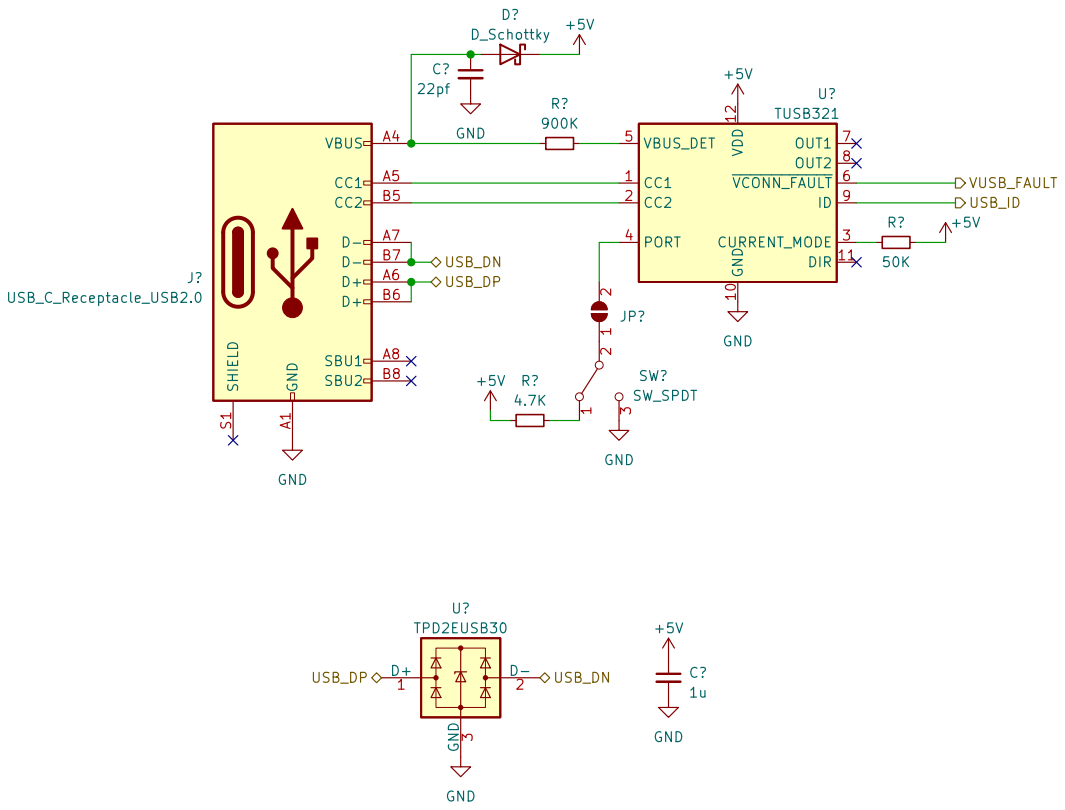
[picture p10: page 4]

TODO: Change to Full DRP USB implementation

File: FlySensei_Stack_RPi_PiUSB.kicad_sch Sheet: /USB/ George Mason University

Id: 4/8 Title: FlySensei RPi Stack - USB Connection

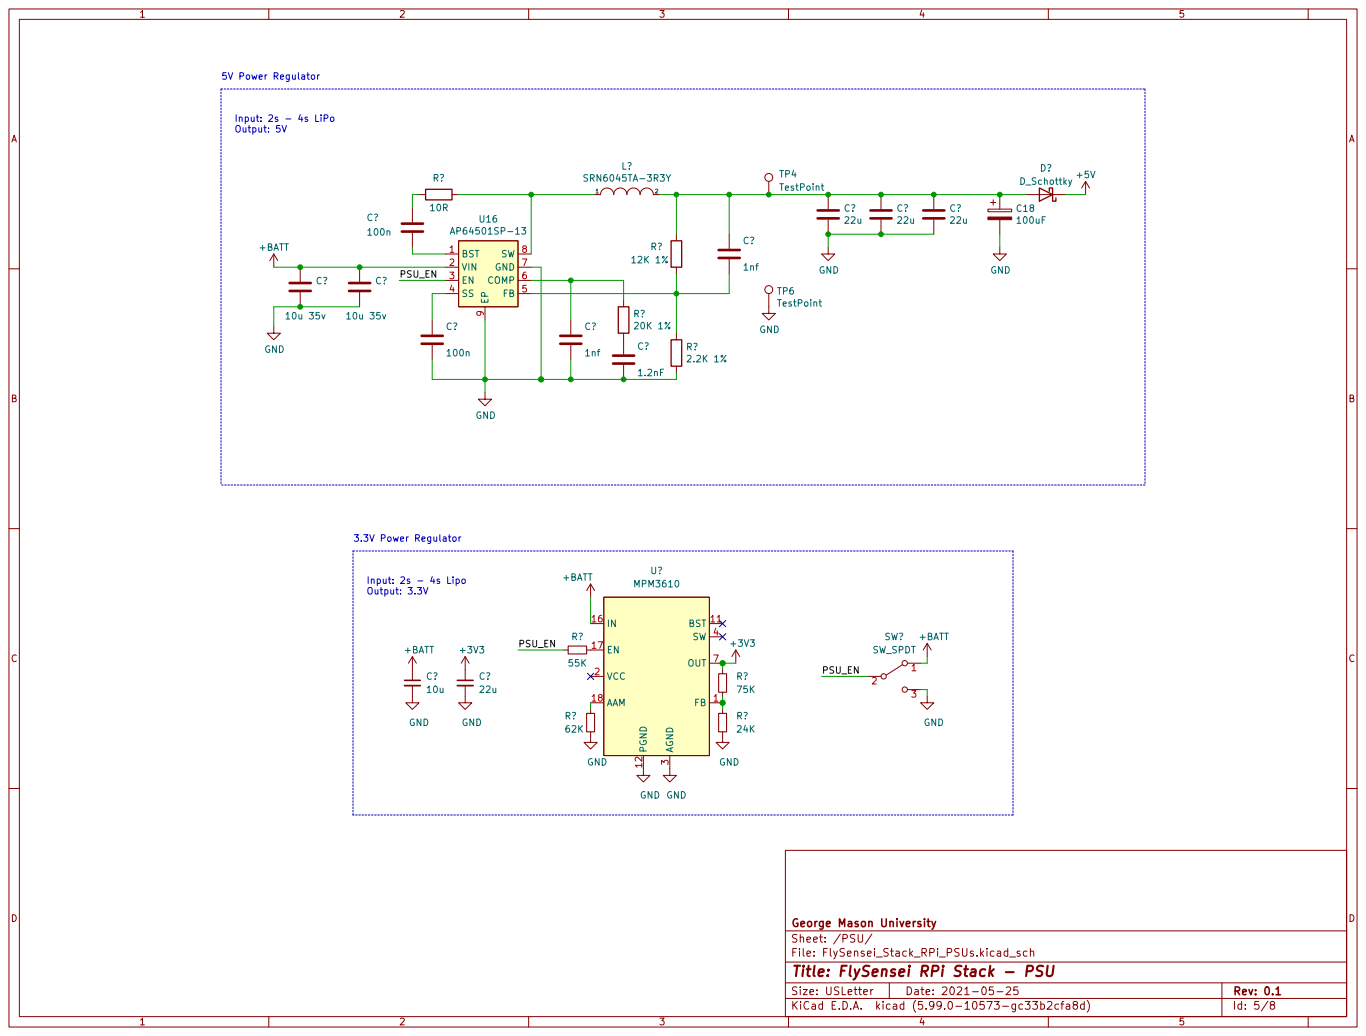
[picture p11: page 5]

File: FlySensei_Stack_RPi_PSUs.kicad_sch Sheet: /PSU/ George Mason University

Id: 5/8 Title: FlySensei RPi Stack - PSU

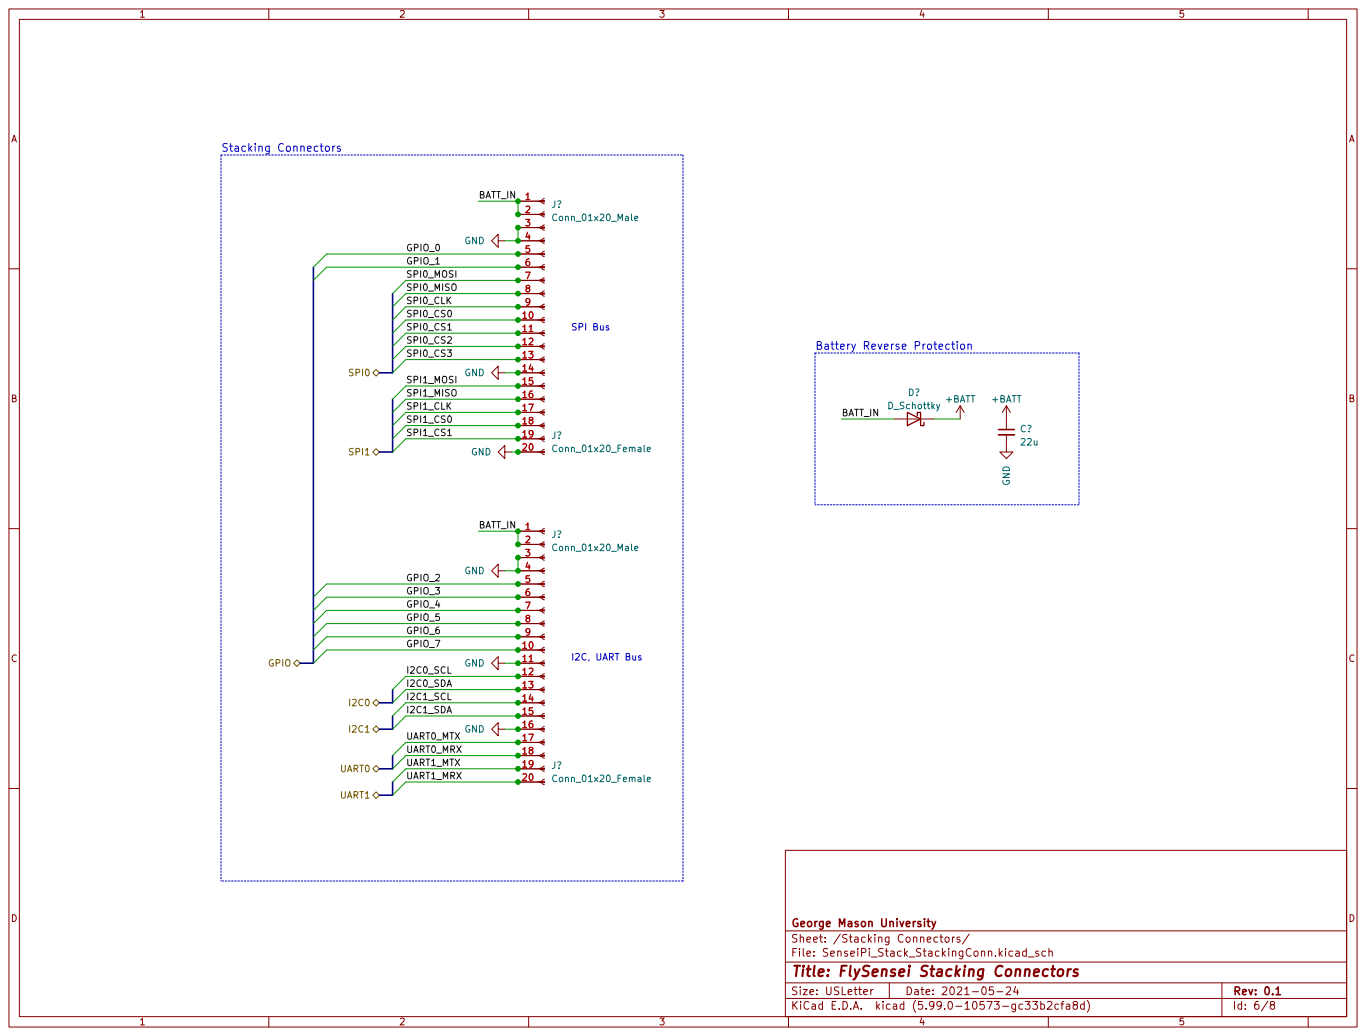
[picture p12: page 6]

George Mason University
Sheet: /Stacking Connectors/
File: SenseiPi_Stack_StackingConn.kicad_sch
Id: 6/8 Title: FlySensei Stacking Connectors


George Mason University GND

Sheet: /High Speed Interfaces/
File: FlySensei_Stack_RPi_HSS_Intr.kicad_sch
Id: 7/8 Title: FlySensei RPi Stack - High Speed Connectors


File: FlySensei_Stack_RPi_SDCard.kicad_sch Sheet: /SD Card/ George Mason University C?

Id: 8/8 Title: FlySensei RPi Stack - SD Card































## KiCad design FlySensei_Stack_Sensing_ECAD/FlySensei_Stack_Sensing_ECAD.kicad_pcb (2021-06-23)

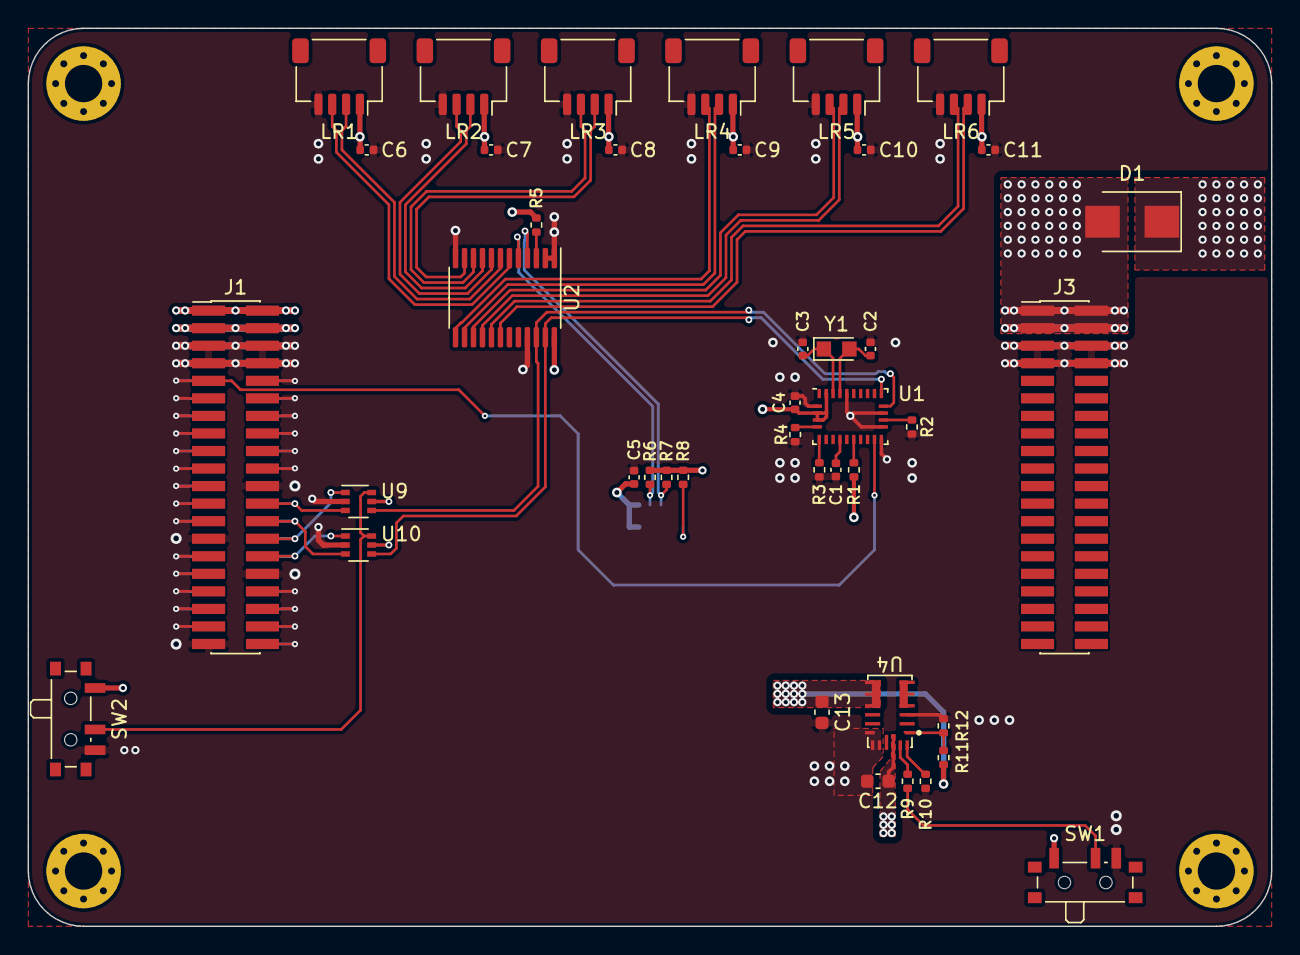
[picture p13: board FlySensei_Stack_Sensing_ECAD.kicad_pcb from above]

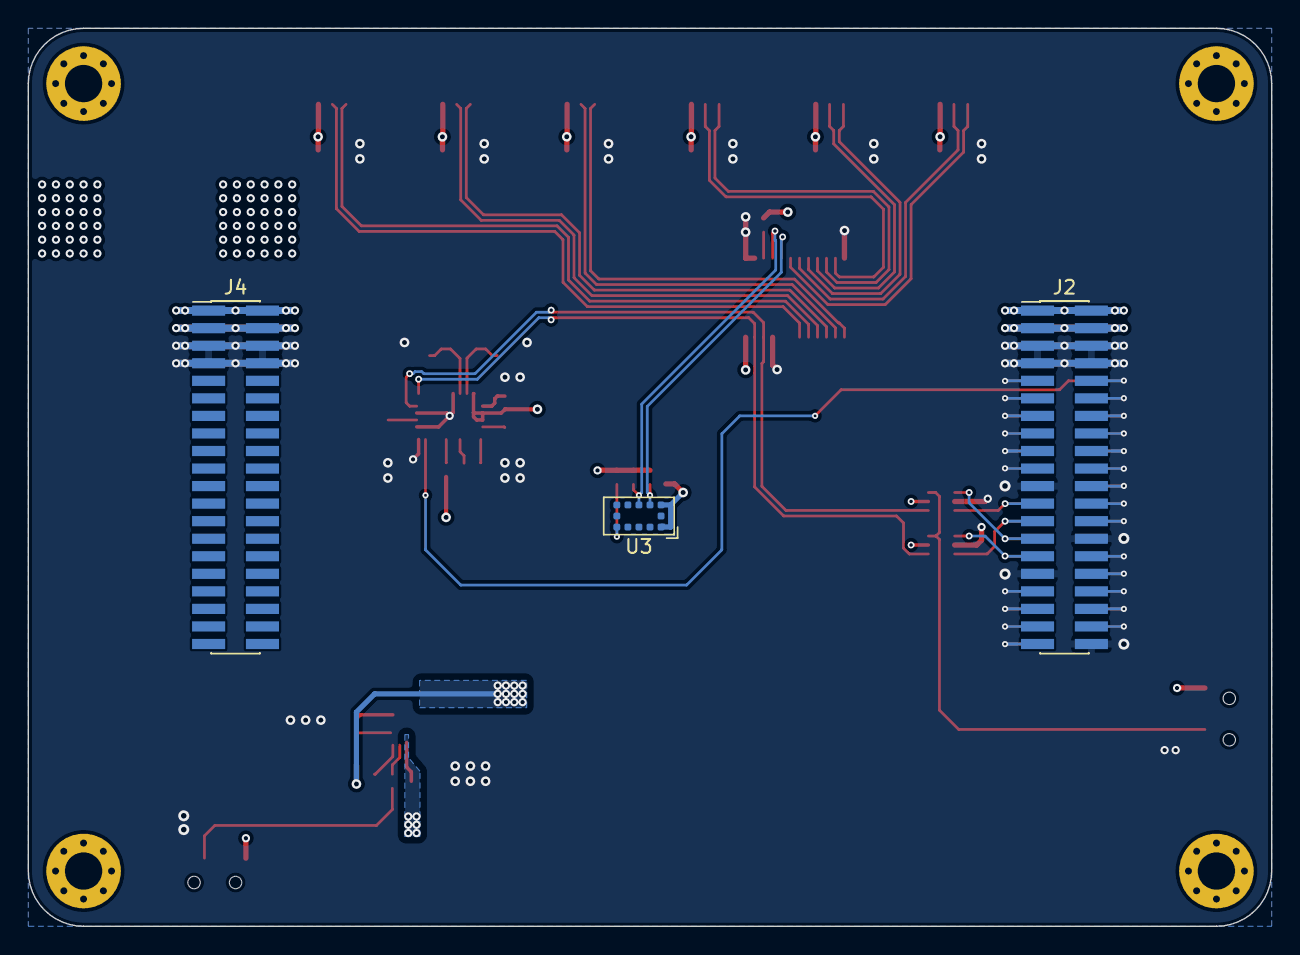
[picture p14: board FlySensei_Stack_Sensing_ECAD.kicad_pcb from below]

Board: 4 copper layers, 90.0 x 65.0 mm, 49 parts (3 on the bottom side), 62 nets.

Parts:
C1, C4, C5, C6, C7, C8, C9, C10, C11: 0u1F; C_0402_1005Metric
C2, C3: 22pF; C_0402_1005Metric
C12: 10uF; C_0603_1608Metric
C13: 22uF; C_0603_1608Metric
D1: D_SCHTKY; D_SMB
H1, H2, H3, H4: MountingHole; MountingHole_2.7mm_M2.5_Pad_Via
J1, J3: Conn_02x20_Odd_Even_Male; PinHeader_2x20_P1.27mm_Vertical_SMD
J2, J4: Conn_02x20_Odd_Even_Female; PinHeader_2x20_P1.27mm_Vertical_SMD
LR1, LR2, LR3, LR4, LR5, LR6: JST_SH_SM04; JST_SH_SM04B-SRSS-TB_1x04-1MP_P1.00mm_Horizontal
R1, R5: 0K; R_0402_1005Metric
R2, R3, R4, R6, R7, R8: 10K; R_0402_1005Metric
R9: 55K; R_0402_1005Metric
R10: 62K; R_0402_1005Metric
R11: 75K; R_0402_1005Metric
R12: 24K; R_0402_1005Metric
SW1, SW2: SW_SPDT; SW_SPDT_PCM12
U1: BNO055; LGA-28_5.2x3.8mm_P0.5mm
U2: TCA9548APWR; TSSOP-24_4.4x7.8mm_P0.65mm
U3: VL53L0CXV0DH_1; ST_VL53L1x
U4: MPM3610; MPM3610_QFN-20_5x3mm
U9, U10: TS5A3159ADCKR; SOT-363_SC-70-6
Y1: Crystal; Crystal_SMD_2012-2Pin_2.0x1.2mm_HandSoldering

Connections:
+3V3: C4.1, C5.1, C6.1, C7.1, C8.1, C9.1, C10.1, C11.1, C13.1, LR1.1, LR2.1, LR3.1, LR4.1, LR5.1, LR6.1, R1.1, R5.2, R6.1, R7.1, R8.1, R11.1, SW2.1 (A), U1.3 (VDD), U1.4 (~BOOT_LOAD_PIN), U1.28 (VDDIO), U2.24 (VCC), U3.1 (AVDDVCSEL), U3.11 (AVDD), U4.7 (OUT), U4.8 (OUT), U4.9 (OUT), U9.5 (V+), U10.5 (V+)
+BATT: C12.1, D1.1 (K), SW1.1 (A), U4.16 (IN)
/I2C Mux/I2C0.SCL: J1.24, J2.23, U9.3
/I2C Mux/I2C0.SDA: J1.26, J2.25, U10.3
/I2C Mux/I2C1.SCL: J1.28, J2.27, U9.1
/I2C Mux/I2C1.SDA: J1.30, J2.29, U10.1
/I2C Mux/I2C_SCL: U1.19 (COM1), U2.22 (SCL), U9.4
/I2C Mux/I2C_SDA: U1.20 (COM0), U2.23 (SDA), U10.4
/I2C Mux/I2C_SEL: SW2.2 (B), U9.6, U10.6
/LIDAR/I2C1_SCL: LR1.2, U2.7 (SC1)
/LIDAR/I2C1_SDA: LR1.3, U2.6 (SD1)
/LIDAR/I2C2_SCL: LR2.2, U2.9 (SC2)
/LIDAR/I2C2_SDA: LR2.3, U2.8 (SD2)
/LIDAR/I2C3_SCL: LR3.2, U2.11 (SC3)
/LIDAR/I2C3_SDA: LR3.3, U2.10 (SD3)
/LIDAR/I2C4_SCL: LR4.2, U2.14 (SC4)
/LIDAR/I2C4_SDA: LR4.3, U2.13 (SD4)
/LIDAR/I2C5_SCL: LR5.2, U2.16 (SC5)
/LIDAR/I2C5_SDA: LR5.3, U2.15 (SD5)
/LIDAR/I2C6_SCL: LR6.2, U2.18 (SC6)
/LIDAR/I2C6_SDA: LR6.3, U2.17 (SD6)
/PSU/3V3_EN: R9.1, SW1.2 (B)
/Stacking Connector/BATT_IN: D1.2 (A), J1.1, J1.2, J1.3, J1.4, J2.1, J2.2, J2.3, J2.4, J3.1, J3.2, J3.3, J3.4, J4.1, J4.2, J4.3, J4.4
/Stacking Connector/GPIO0: J1.9, J2.10, U1.14 (INT)
/Stacking Connector/GPIO1: J1.11, J2.12
/Stacking Connector/GPIO2: J1.10, J2.9
/Stacking Connector/GPIO3: J1.12, J2.11
/Stacking Connector/GPIO4: J1.14, J2.13
/Stacking Connector/GPIO5: J1.16, J2.15
/Stacking Connector/GPIO6: J1.18, J2.17
/Stacking Connector/GPIO7: J1.20, J2.19
/Stacking Connector/SPI0.CLK: J1.17, J2.18
/Stacking Connector/SPI0.CS0: J1.19, J2.20
/Stacking Connector/SPI0.CS1: J1.21, J2.22
/Stacking Connector/SPI0.CS2: J1.23, J2.24
/Stacking Connector/SPI0.CS3: J1.25, J2.26
/Stacking Connector/SPI0.MISO: J1.15, J2.16
/Stacking Connector/SPI0.MOSI: J1.13, J2.14
/Stacking Connector/SPI1.CLK: J1.33, J2.34
/Stacking Connector/SPI1.CS0: J1.35, J2.36
/Stacking Connector/SPI1.CS1: J1.37, J2.38
/Stacking Connector/SPI1.MISO: J1.31, J2.32
/Stacking Connector/SPI1.MOSI: J1.29, J2.30
/Stacking Connector/UART0.RX: J1.36, J2.35
/Stacking Connector/UART0.TX: J1.34, J2.33
/Stacking Connector/UART1.RX: J1.40, J2.39
/Stacking Connector/UART1.TX: J1.38, J2.37
GND: C1.1, C2.2, C3.2, C4.2, C5.2, C6.2, C7.2, C8.2, C9.2, C10.2, C11.2, C12.2, C13.2, J1.5, J1.6, J1.7, J1.8, J1.22, J1.27, J1.32, J1.39, J2.5, J2.6, J2.7, J2.8, J2.21, J2.28, J2.31, J2.40, J3.5, J3.6, J3.7, J3.8, J4.5, J4.6, J4.7, J4.8, LR1.4, LR2.4, LR3.4, LR4.4, LR5.4, LR6.4, R2.1, R3.2, R4.2, R10.2, R12.2, SW1.3 (C), SW2.3 (C), U1.2 (GND), U1.15 (GNDIO), U1.16 (GNDIO), U1.18 (COM2), U1.25 (GNDIO), U2.1 (A0), U2.2 (A1), U2.12 (GND), U2.21 (A2), U3.2 (AVSSVCSEL), U3.3 (GND), U3.4 (GND), U3.6 (GND), U3.12 (GND), U4.3 (AGND), U4.12 (PGND), U4.13 (PGND), U4.14 (PGND), U9.2 (GND), U10.2 (GND)
unnamed: C1.2, U1.9 (CAP)
unnamed: C2.1, U1.26 (XOUT32), Y1.2
unnamed: C3.1, U1.27 (XIN32), Y1.1
unnamed: R1.2, U1.11 (~RESET)
unnamed: R2.2, U1.17 (COM3)
unnamed: R3.1, U1.6 (PS0)
unnamed: R4.1, U1.5 (PS1)
unnamed: R5.1, U2.3 (~RESET)
unnamed: R6.2, U2.5 (SC0), U3.10 (SCL)
unnamed: R7.2, U2.4 (SD0), U3.9 (SDA)
unnamed: R8.2, U3.5 (XSHUT)
unnamed: R9.2, U4.17 (EN)
unnamed: R10.1, U4.18 (AAM)
unnamed: R11.2, R12.1, U4.1 (FB)

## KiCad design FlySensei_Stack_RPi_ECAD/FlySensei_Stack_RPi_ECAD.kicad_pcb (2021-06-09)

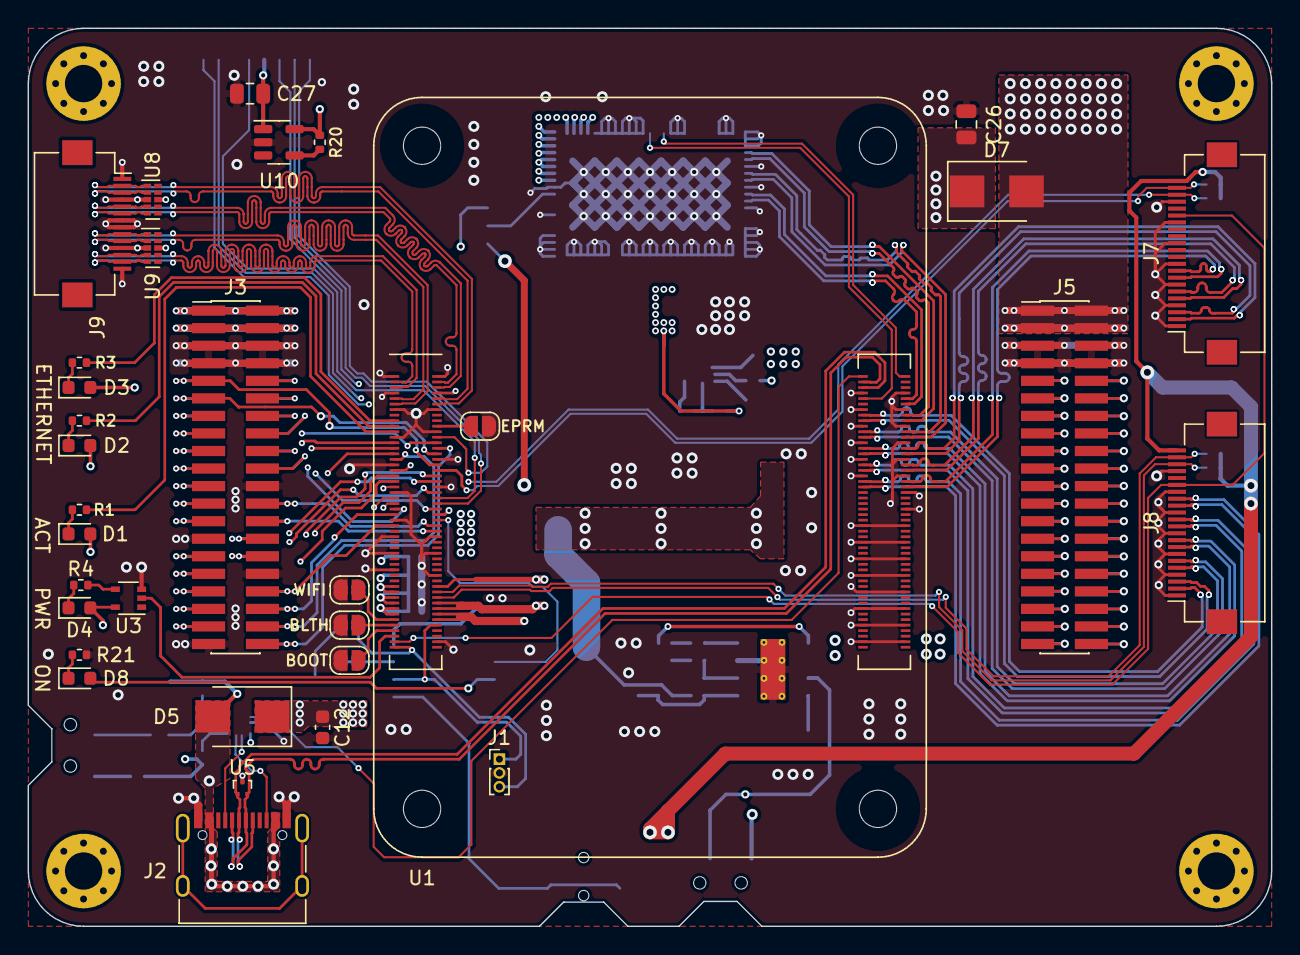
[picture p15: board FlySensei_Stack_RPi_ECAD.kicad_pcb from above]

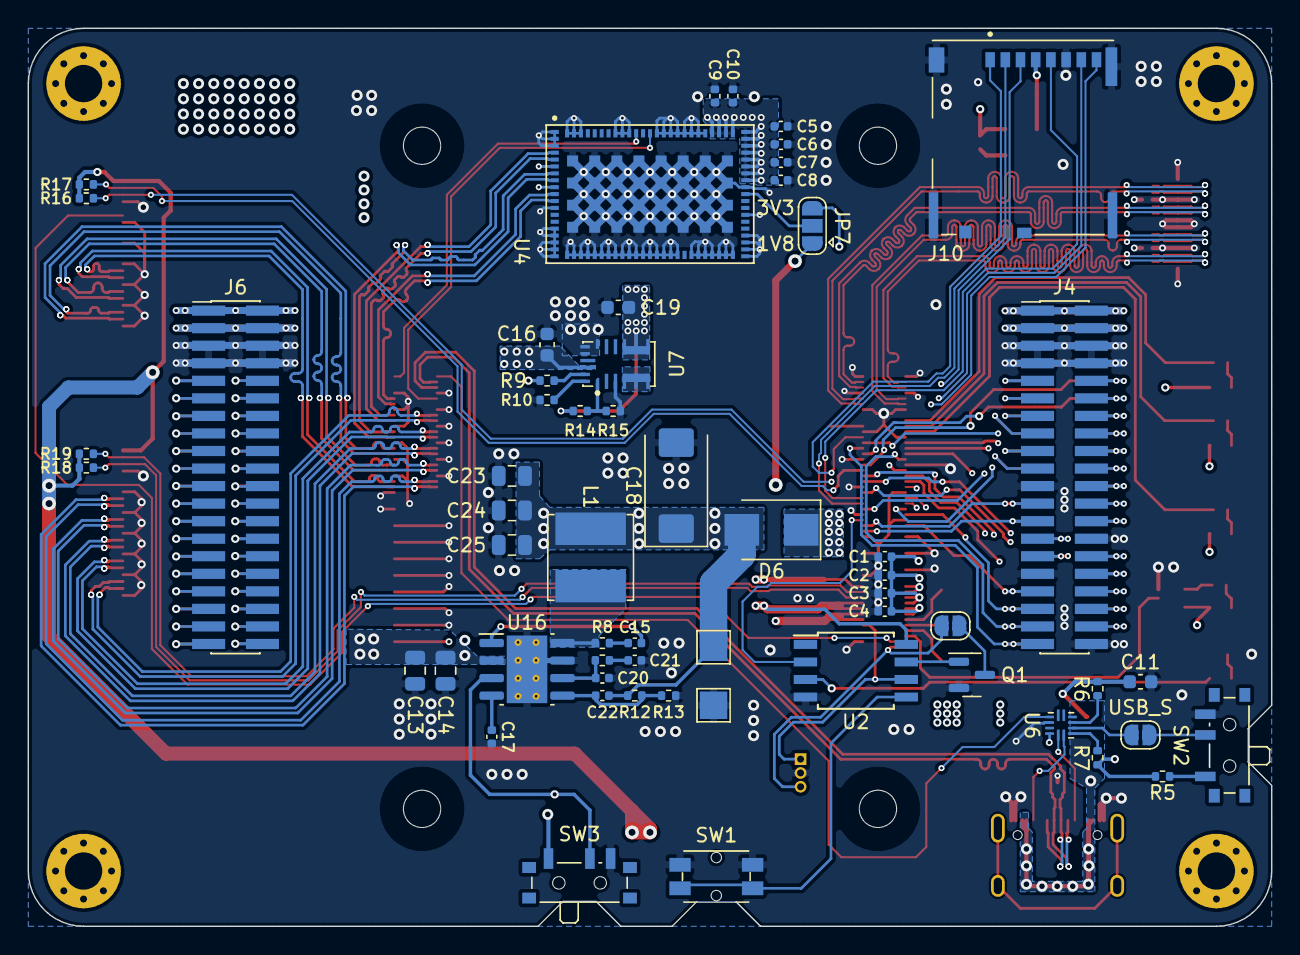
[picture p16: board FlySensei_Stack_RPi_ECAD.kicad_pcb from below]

Board: 4 copper layers, 90.0 x 65.0 mm, 95 parts (58 on the bottom side), 125 nets.

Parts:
C1, C2, C3, C4: 0u1 16V; C_0402_1005Metric
C5, C6, C7, C8, C9, C10: 0u1 6.3V; C_0402_1005Metric
C11, C19: 22u 16V; C_0603_1608Metric
C12: 1u 16V; C_0603_1608Metric
C13, C14: 10u 35v; C_0805_2012Metric
C15, C17: 100n 35V; C_0402_1005Metric
C16: 10u 35V; C_0603_1608Metric
C18: 100uF; CP_EIA-7343-31_Kemet-D
C20, C22: 1nf 16V; C_0402_1005Metric
C21: 1.2nF 16V; C_0402_1005Metric
C23, C24, C25: 22u 16V; C_0805_2012Metric
C26: 22u; C_0805_2012Metric
C27: 10u; C_0805_2012Metric
D1, D2: LED_GRN; LED_0603_1608Metric
D3: LED_AMB; LED_0603_1608Metric
D4: LED_RED; LED_0603_1608Metric
D5, D6, D7: D_Schottky; D_SMB
D8: LED_WHT; LED_0603_1608Metric
H1, H2, H3, H4: MountingHole; MountingHole_2.7mm_M2.5_Pad_Via
J1: Conn_01x03; PinHeader_1x03_P1.00mm_Vertical
J2: USB_C_Receptacle_USB2.0; USB_C_Receptacle_XKB_U262-16XN-4BVC11
J3, J5: Conn_02x20_Odd_Even_Male; PinHeader_2x20_P1.27mm_Vertical_SMD
J4, J6: Conn_02x20_Odd_Even_Female; PinHeader_2x20_P1.27mm_Vertical_SMD
J7, J8: Conn_01x22_Female; Hirose_FH12-22S-0.5SH_1x22-1MP_P0.50mm_Horizontal
J9: Conn_01x14_Female; Hirose_FH12-14S-0.5SH_1x14-1MP_P0.50mm_Horizontal
J10: Micro_SD_Card_Det; SDCARD_MOLEX_503398-1892
JP1, JP2, JP3, JP4, JP5, JP6: SolderJumper_2_Open; SolderJumper-2_P1.3mm_Open_RoundedPad1.0x1.5mm
JP7: SolderJumper_3_Open; SolderJumper-3_P1.3mm_Open_RoundedPad1.0x1.5mm
L1: SRN6045TA-3R3Y; L_Bourns_SRN6045TA
Q1: Q_NMOS_GSD; SOT-23
R1, R2, R3, R4: 270R; R_0402_1005Metric
R5: 4.7K; R_0402_1005Metric
R6: 900K; R_0402_1005Metric
R7: 50K; R_0402_1005Metric
R8: 10R; R_0402_1005Metric
R9: 55K; R_0402_1005Metric
R10: 62K; R_0402_1005Metric
R11: 20K 1%; R_0402_1005Metric
R12: 12K 1%; R_0402_1005Metric
R13: 2.2K 1%; R_0402_1005Metric
R14: 75K; R_0402_1005Metric
R15: 24K; R_0402_1005Metric
R16, R17, R18, R19: 10K; R_0402_1005Metric
R20: 12K; R_0402_1005Metric
R21: 480; R_0402_1005Metric
SW1: SW_SPST; Panasonic_EVQPUL_EVQPUC
SW2, SW3: SW_SPDT; SW_SPDT_PCM12
TP4, TP6: TestPoint; TestPoint_Pad_2.0x2.0mm
U1: ComputeModule4-CM4; Raspberry-Pi-4-Compute-Module
U2: ATtiny85V-10S; SOIC-8W_5.3x5.3mm_P1.27mm
U3: 74LVC1G07; SOT-353_SC-70-5
U4: G313-06329-00
U5: TPD2EUSB30; Texas_DRT-3
U6: TUSB321; Texas_X2QFN-12_1.6x1.6mm_P0.4mm
U7: MPM3610; MPM3610_QFN-20_5x3mm
U8, U9: TPD4EUSB30; USON-10_2.5x1.0mm_P0.5mm
U10: RT9742GGJ5; SOT-23-5
U16: AP64501SP-13; SOIC-8-1EP_3.9x4.9mm_P1.27mm_EP2.95x4.9mm_Mask2.71x3.4mm_Th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

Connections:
+1V8_RPI: JP7.1 (A), U1.88 (+1.8v_(Output)), U1.90 (+1.8v_(Output))
+3V3: C5.1, C6.1, C7.1, C8.1, C9.1, C10.1, C19.1, R14.1, U4.56 (VIN), U4.57 (VIN), U4.58 (VIN), U4.59 (VIN), U4.60 (VIN), U4.61 (VIN), U4.62 (VIN), U4.63 (VIN), U4.64 (VIN), U4.65 (VIN), U4.66 (VIN), U4.67 (VIN), U7.7 (OUT), U7.8 (OUT), U7.9 (OUT)
+3V3_RPI: D1.2 (A), D2.2 (A), D3.2 (A), D4.2 (A), J7.22, J8.22, JP7.3 (B), R16.1, R17.1, R18.1, R19.1, R20.1, U1.78 (GPIO_VREF(1.8v/3.3v_Input)), U1.84 (+3.3v_(Output)), U1.86 (+3.3v_(Output)), U2.8 (VCC), U3.5 (VCC), U10.5 (IN)
+5V: C1.1, C2.1, C3.1, C4.1, C12.1, D5.1 (K), D6.1 (K), R5.2, R7.1, U1.77 (+5v_(Input)), U1.79 (+5v_(Input)), U1.81 (+5v_(Input)), U1.83 (+5v_(Input)), U1.85 (+5v_(Input)), U1.87 (+5v_(Input)), U6.12 (VDD)
+BATT: C13.1, C14.1, C16.1, C26.1, D7.1 (K), SW3.1 (A), U7.16 (IN), U16.2 (VIN)
/AI/CORL_PCIE_CLK_N: U1.112 (PCIe_CLK_N), U4.10 (PCIE_REFCLK_N)
/AI/CORL_PCIE_CLK_P: U1.110 (PCIe_CLK_P), U4.11 (PCIE_REFCLK_P)
/AI/CORL_PCIE_NCLKREQ: U1.102 (PCIe_CLK_nREQ), U4.78 (CLKREQ)
/AI/CORL_PCIE_NRST: U1.109 (PCIe_nRST), U4.76 (RST)
/AI/CORL_PCIE_RX_N: U1.124 (PCIe_TX_N), U4.8 (PCIE_RX_N)
/AI/CORL_PCIE_RX_P: U1.122 (PCIe_TX_P), U4.7 (PCIE_RX_P)
/AI/CORL_PCIE_TX_N: U1.118 (PCIe_RX_N), U4.4 (PCIE_TX_N)
/AI/CORL_PCIE_TX_P: U1.116 (PCIe_RX_P), U4.5 (PCIE_TX_P)
/High Speed Interfaces/CAM0_MIPI.C_N: J7.8, U1.140 (CAM0_C_N)
/High Speed Interfaces/CAM0_MIPI.C_P: J7.9, U1.142 (CAM0_C_P)
/High Speed Interfaces/CAM0_MIPI.D0_N: J7.2, U1.128 (CAM0_D0_N)
/High Speed Interfaces/CAM0_MIPI.D0_P: J7.3, U1.130 (CAM0_D0_P)
/High Speed Interfaces/CAM0_MIPI.D1_N: J7.5, U1.134 (CAM0_D1_N)
/High Speed Interfaces/CAM0_MIPI.D1_P: J7.6, U1.136 (CAM0_D1_P)
/High Speed Interfaces/CAM0_SCL: J7.20, R16.2, U1.35 (ID_SC)
/High Speed Interfaces/CAM0_SDA: J7.21, R17.2, U1.36 (ID_SD)
/High Speed Interfaces/CAM1_MIPI.C_N: J8.8, U1.127 (CAM1_C_N)
/High Speed Interfaces/CAM1_MIPI.C_P: J8.9, U1.129 (CAM1_C_P)
/High Speed Interfaces/CAM1_MIPI.D0_N: J8.2, U1.115 (CAM1_D0_N)
/High Speed Interfaces/CAM1_MIPI.D0_P: J8.3, U1.117 (CAM1_D0_P)
/High Speed Interfaces/CAM1_MIPI.D1_N: J8.5, U1.121 (CAM1_D1_N)
/High Speed Interfaces/CAM1_MIPI.D1_P: J8.6, U1.123 (CAM1_D1_P)
/High Speed Interfaces/CAM1_MIPI.D2_N: J8.11, U1.133 (CAM1_D2_N)
/High Speed Interfaces/CAM1_MIPI.D2_P: J8.12, U1.135 (CAM1_D2_P)
/High Speed Interfaces/CAM1_MIPI.D3_N: J8.14, U1.139 (CAM1_D3_N)
/High Speed Interfaces/CAM1_MIPI.D3_P: J8.15, U1.141 (CAM1_D3_P)
/High Speed Interfaces/CAM1_SCL: J8.20, R18.2, U1.80 (SCL0)
/High Speed Interfaces/CAM1_SDA: J8.21, R19.2, U1.82 (SDA0)
/High Speed Interfaces/CAM_GPIO: J7.17, J8.17, U1.97 (Camera_GPIO)
/High Speed Interfaces/ETH.0_N: J9.3, U1.10 (Ethernet_Pair0_N), U8.2 (D1-)
/High Speed Interfaces/ETH.0_P: J9.2, U1.12 (Ethernet_Pair0_P), U8.1 (D1+)
/High Speed Interfaces/ETH.1_N: J9.6, U1.4 (Ethernet_Pair1_P), U8.5 (D2-)
/High Speed Interfaces/ETH.1_P: J9.5, U1.6 (Ethernet_Pair1_N), U8.4 (D2+)
/High Speed Interfaces/ETH.2_N: J9.10, U1.9 (Ethernet_Pair2_N), U9.2 (D1-)
/High Speed Interfaces/ETH.2_P: J9.9, U1.11 (Ethernet_Pair2_P), U9.1 (D1+)
/High Speed Interfaces/ETH.3_N: J9.13, U1.3 (Ethernet_Pair3_P), U9.5 (D2-)
/High Speed Interfaces/ETH.3_P: J9.12, U1.5 (Ethernet_Pair3_N), U9.4 (D2+)
/PSU/PSU_EN: R9.1, SW3.2 (B), U16.3 (EN)
/RPi_CM4/ETH_nLED1: R2.2, U1.19 (Ethernet_nLED1(3.3v))
/RPi_CM4/ETH_nLED2: R3.2, U1.17 (Ethernet_nLED2(3.3v))
/RPi_CM4/GPIO_0: J3.9, J4.10, U1.34 (GPIO5)
/RPi_CM4/GPIO_1: J3.11, J4.12, U1.30 (GPIO6)
/RPi_CM4/GPIO_2: J3.10, J4.9
/RPi_CM4/GPIO_3: J3.12, J4.11
/RPi_CM4/GPIO_4: J3.14, J4.13
/RPi_CM4/GPIO_5: J3.16, J4.15
/RPi_CM4/GPIO_6: J3.18, J4.17
/RPi_CM4/GPIO_7: J3.20, J4.19
/RPi_CM4/I2C0.SCL: J3.24, J4.23, U1.56 (GPIO3)
/RPi_CM4/I2C0.SDA: J3.26, J4.25, U1.58 (GPIO2)
/RPi_CM4/RPI_GLOBL_EN: J1.3, JP5.2 (B), U1.99 (Global_EN)
/RPi_CM4/RPI_RUN_PG: J1.1, U1.92 (RUN_PG), U2.6 (PB1)
/RPi_CM4/RPI_SHTDWN: U1.54 (GPIO4), U2.2 (XTAL1/PB3)
/RPi_CM4/RPI_nLED_ACT: R1.2, U1.21 (PI_nLED_Activity)
/RPi_CM4/RPI_nLED_PWR: U1.95 (PI_nLED_PWR), U3.2
/RPi_CM4/SD_D_CLK: J10.5 (CLK), U1.46 (GPIO22)
/RPi_CM4/SD_D_CMD: J10.3 (CMD), U1.47 (GPIO23)
/RPi_CM4/SD_D_DAT0: J10.7 (DAT0), U1.45 (GPIO24)
/RPi_CM4/SD_D_DAT1: J10.8 (DAT1), U1.41 (GPIO25)
/RPi_CM4/SD_D_DAT2: J10.1 (DAT2), U1.24 (GPIO26)
/RPi_CM4/SD_D_DAT3: J10.2 (DAT3/CD), U1.48 (GPIO27)
/RPi_CM4/SPI0.CLK: J3.17, J4.18, U1.25 (GPIO21)
/RPi_CM4/SPI0.CS0: J3.19, J4.20, U1.49 (GPIO18)
/RPi_CM4/SPI0.CS1: J3.21, J4.22, U1.50 (GPIO17)
/RPi_CM4/SPI0.CS2: J3.23, J4.24, U1.29 (GPIO16)
/RPi_CM4/SPI0.CS3: J3.25, J4.26
/RPi_CM4/SPI0.MISO: J3.15, J4.16, U1.26 (GPIO19)
/RPi_CM4/SPI0.MOSI: J3.13, J4.14, U1.27 (GPIO20)
/RPi_CM4/SPI1.CLK: J3.33, J4.34, U1.38 (GPIO11)
/RPi_CM4/SPI1.CS0: J3.35, J4.36, U1.39 (GPIO8)
/RPi_CM4/SPI1.CS1: J3.37, J4.38, U1.37 (GPIO7)
/RPi_CM4/SPI1.MISO: J3.31, J4.32, U1.40 (GPIO9)
/RPi_CM4/SPI1.MOSI: J3.29, J4.30, U1.44 (GPIO10)
/RPi_CM4/UART0.RX: J3.36, J4.35, U1.51 (GPIO15)
/RPi_CM4/UART0.TX: J3.34, J4.33, U1.55 (GPIO14)
/RPi_CM4/UART1.RX: J3.40, J4.39, U1.28 (GPIO13)
/RPi_CM4/UART1.TX: J3.38, J4.37, U1.31 (GPIO12)
/RPi_CM4/USB_DN: J2.A7 (D-), J2.B7 (D-), U1.103 (USB2_N), U5.2 (D-)
/RPi_CM4/USB_DP: J2.A6 (D+), J2.B6 (D+), U1.105 (USB2_P), U5.1 (D+)
/RPi_CM4/USB_ID: U1.101 (USB_OTG_ID), U6.9 (ID)
/SD Card/SD_PWR: C27.1, J10.4 (VDD), U10.1 (OUT)
/Stacking Connectors/BATT_IN: D7.2 (A), J3.1, J3.2, J3.3, J3.4, J4.1, J4.2, J4.3, J4.4, J5.1, J5.2, J5.3, J5.4, J6.1, J6.2, J6.3, J6.4
/Stacking Connectors/I2C1.SCL: J3.28, J4.27
/Stacking Connectors/I2C1.SDA: J3.30, J4.29
GND: C1.2, C2.2, C3.2, C4.2, C5.2, C6.2, C7.2, C8.2, C9.2, C10.2, C11.2, C12.2, C13.2, C14.2, C16.2, C17.2, C18.2, C19.2, C20.2, C21.2, C23.2, C24.2, C25.2, C26.2, C27.2, J1.2, J2.A1 (GND), J2.A12 (GND), J2.B1 (GND), J2.B12 (GND), J3.5, J3.6, J3.7, J3.8, J3.22, J3.27, J3.32, J3.39, J4.5, J4.6, J4.7, J4.8, J4.21, J4.28, J4.31, J4.40, J5.5, J5.6, J5.7, J5.8, J6.5, J6.6, J6.7, J6.8, J7.1, J7.4, J7.7, J7.10, J7.13, J7.16, J7.19, J8.1, J8.4, J8.7, J8.10, J8.13, J8.16, J8.19, J9.1, J9.4, J9.7, J9.8, J9.11, J9.14, J10.6 (VSS), J10.11 (SHIELD), JP1.1 (A), JP2.1 (A), JP3.1 (A), JP4.1 (A), Q1.2 (S), R10.2, R13.2, R15.2, R21.2, SW1.2 (B), SW2.3 (C), SW3.3 (C), TP6.1, U1.1 (GND), U1.2 (GND), U1.7 (GND), U1.8 (GND), U1.13 (GND), U1.14 (GND), U1.22 (GND), U1.23 (GND), U1.32 (GND), U1.33 (GND), U1.42 (GND), U1.43 (GND), U1.52 (GND), U1.53 (GND), U1.59 (GND), U1.60 (GND), U1.65 (GND), U1.66 (GND), U1.71 (GND), U1.74 (GND), U1.98 (GND), U1.107 (GND), U1.108 (GND), U1.113 (GND), U1.114 (GND), U1.119 (GND), U1.120 (GND), U1.125 (GND), U1.126 (GND), U1.131 (GND), U1.132 (GND), U1.137 (GND), U1.138 (GND), U1.144 (GND), U1.150 (GND), U1.155 (GND), U1.156 (GND), U1.161 (GND), U1.162 (GND), U1.167 (GND), U1.168 (GND), U1.173 (GND), U1.174 (GND), U1.179 (GND), U1.180 (GND), U1.185 (GND), U1.186 (GND), U1.191 (GND), U1.192 (GND), U1.197 (GND), U1.198 (GND), U2.4 (GND), U3.3 (GND), U4.1 (GND), U4.2 (GND), U4.3 (GND), U4.6 (GND), U4.9 (GND), U4.12 (GND), U4.15 (GND), U4.16 (GND), U4.17 (GND), U4.18 (GND), U4.19 (GND), U4.20 (GND), U4.21 (GND), U4.22 (GND), U4.23 (GND), U4.24 (GND), U4.25 (GND), U4.26 (GND), U4.27 (GND), U4.28 (GND), U4.29 (GND), U4.30 (GND), U4.31 (GND), U4.32 (GND), U4.33 (GND), U4.34 (GND), U4.35 (GND), U4.36 (GND), U4.38 (GND), U4.39 (GND), U4.40 (GND), U4.41 (GND), U4.42 (GND), U4.43 (GND), U4.44 (GND), U4.45 (GND), U4.46 (GND), U4.47 (GND), U4.48 (GND), U4.51 (GND), U4.55 (GND), U4.68 (GND), U4.69 (GND), U4.70 (GND), U4.71 (GND), U4.72 (GND), U4.73 (GND), U4.74 (GND), U4.75 (GND), U4.79 (GND), U4.80 (GND), U4.81 (GND), U4.86 (GND), U4.87 (GND), U4.88 (GND), U4.89 (GND), U4.90 (GND), U4.91 (GND), U4.92 (GND), U4.93 (GND), U4.94 (GND), U4.95 (GND), U4.96 (GND), U4.97 (GND), U4.98 (GND), U4.99 (GND), U4.100 (GND), U4.101 (GND), U4.102 (GND), U4.103 (GND), U4.104 (GND), U4.105 (GND), U4.106 (GND), U4.107 (GND), U4.108 (GND), U4.109 (GND), U4.110 (GND), U4.111 (GND), U4.112 (GND), U4.113 (GND), U4.114 (GND), U4.115 (GND), U4.116 (GND), U4.117 (GND), U4.118 (GND), U4.119 (GND), U4.120 (GND), U5.3 (GND), U6.10 (GND), U7.3 (AGND), U7.12 (PGND), U7.13 (PGND), U7.14 (PGND), U8.3 (GND), U8.8 (GND), U9.3 (GND), U9.8 (GND), U10.2 (GND), U16.7 (GND), U16.9 (EP)
unnamed: C11.1, D5.2 (A), J2.A4 (VBUS), J2.A9 (VBUS), J2.B4 (VBUS), J2.B9 (VBUS), R6.2
unnamed: C15.1, R8.2
unnamed: C15.2, U16.1 (BST)
unnamed: C17.1, U16.4 (SS)
unnamed: C18.1, C22.1, C23.1, C24.1, C25.1, D6.2 (A), L1.2, R12.1, TP4.1
unnamed: C20.1, R11.1, U16.6 (COMP)
unnamed: C21.1, R11.2
unnamed: C22.2, R12.2, R13.1, U16.5 (FB)
unnamed: D1.1 (K), R1.1
unnamed: D2.1 (K), R2.1
unnamed: D3.1 (K), R3.1
unnamed: D4.1 (K), R4.1
unnamed: D8.1 (K), R21.1
unnamed: D8.2 (A), U2.3 (XTAL2/PB4)
unnamed: J2.A5 (CC1), U6.1 (CC1)
unnamed: J2.B5 (CC2), U6.2 (CC2)
unnamed: JP1.2 (B), U1.93 (nRPIBOOT)
unnamed: JP2.2 (B), U1.20 (EEPROM_nWP)
unnamed: JP3.2 (B), U1.89 (WiFi_nDisable)
unnamed: JP4.2 (B), U1.91 (BT_nDisable)
unnamed: JP5.1 (A), Q1.3 (D)
unnamed: JP6.1 (A), SW2.2 (B)
unnamed: JP6.2 (B), U6.4 (PORT)
unnamed: JP7.2 (C), U4.54 (AON)
unnamed: L1.1, R8.1, U16.8 (SW)
unnamed: Q1.1 (G), U2.7 (PB2)
unnamed: R4.2, U3.4
unnamed: R5.1, SW2.1 (A)
unnamed: R6.1, U6.5 (VBUS_DET)
unnamed: R7.2, U6.3 (CURRENT_MODE)
unnamed: R9.2, U7.17 (EN)
unnamed: R10.1, U7.18 (AAM)
unnamed: R14.2, R15.1, U7.1 (FB)
unnamed: R20.2, U10.4 (EN)
unnamed: SW1.1 (A), U2.5 (AREF/PB0)

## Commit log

2021-05-26 Completed Schematic
    [FlySensei_Stack_RPi_Ai.kicad_sch, FlySensei_Stack_RPi_ECAD.kicad_pcb, FlySensei_Stack_RPi_ECAD.kicad_sch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]
2021-06-02 PCB Design for the Raspberry PI CM4 Board (V0.1)
    [FlySensei_Stack_RPi_Ai.kicad_sch, FlySensei_Stack_RPi_ECAD.kicad_pcb, FlySensei_Stack_RPi_ECAD.kicad_sch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]
2021-06-07 Add PCB design for the actuation board
    [FlySensei_Stack_Actuation_ECAD.kicad_pcb, FlySensei_Stack_Actuation_ECAD.kicad_sch, FlySensei_Stack_Actuation_I2CMux.kicad_sch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]
2021-06-07 Change name of stacking connector schematic file in RPI Stack
    [FlySensei_Stack_StackingConn.kicad_sch]
2021-06-07 Create Template for the Stacking board
    [FlySensei_Stack_StackingConn.kicad_sch, FlySensei_Stack_Template.kicad_pcb, FlySensei_Stack_Template.kicad_sch]
2021-06-09 Add PCB fabrication files
    [FlySensei_Stack_Actuation_ECAD-B_Cu.gbl, FlySensei_Stack_Actuation_ECAD-B_Mask.gbs, FlySensei_Stack_Actuation_ECAD-B_Paste.gbp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]
2021-06-09 Cleanup component values to remain consistent in all skeets
    [FlySensei_Stack_RPi_ECAD.kicad_pcb, FlySensei_Stack_RPi_ECAD.kicad_sch, FlySensei_Stack_RPi_PSUs.kicad_sch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]
2021-06-09 Update part number for fuel gauge IC
    [FlySensei_Stack_Actuation_ECAD.csv, FlySensei_Stack_Actuation_ECAD.kicad_sch, FlySensei_Stack_Actuation_PSU.kicad_sch]
2021-06-15 Rename PCBWay BOM as general BOM
    [FlySensei_Stack_Actuation_ECAD_BOM.xlsx, FlySensei_Stack_Actuation_ECAD_PCBWayBOM.xlsx, FlySensei_Stack_RPi_ECAD_BOM.xlsx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]
2021-06-15 Create IMXRT1170 board Design files
    [FlySensei_Stack_IMXRT1176_ECAD.kicad_pcb, FlySensei_Stack_IMXRT1176_ECAD.kicad_sch]
2021-06-16 Change PWM generation IC package to TSSOP due to availibility
    [FlySensei_Stack_Actuation_ECAD-B_Cu.gbl, FlySensei_Stack_Actuation_ECAD-B_Fab.gbr, FlySensei_Stack_Actuation_ECAD-B_Mask.gbs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]
2021-06-23 PCB Design Added for Sensing Stack
    [FlySensei_Stack_Sensing_ECAD.kicad_pcb, FlySensei_Stack_Sensing_ECAD.kicad_sch, FlySensei_Stack_Sensing_I2CMux.kicad_sch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]
